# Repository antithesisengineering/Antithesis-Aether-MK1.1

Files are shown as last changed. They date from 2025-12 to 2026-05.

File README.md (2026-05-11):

# Antithesis Aether MK1.1

## Description

The Antithesis Aether is a parallel development of the original. It heavily uses 3D printed parts, drastically reducing cost and complexity. It currently has two major options. An all plastic version in which everything, gantry included is plastic. The main drawback with the plastic gantry version is a reduction in rigidity. This will limit acceleration due to excessive deflection. The second option has an aluminum gantry plate, bed bracket, and uses an extrusion on the X axis. It has the same rigidity on the XY as the MK3.1 and still benefits from a reduction in cost and complexity. It also demonstrates identical print quality to the MK3.1.

The build guide is currently a little outdated but will still provide valuable information. It currently doesn't have a section for the assembly of the metal gantry version. 
Please note: The files for the onboard power supply can be found [**HERE**](https://github.com/antithesisengineering/Antithesis-EPP-LOP-Onboard-Power-Supply) 

## 

## Printed Parts

I would recommend printing the parts out of ABS or ASA with the following settings: 3 walls, 40% Gyroid infill. The only exception is the plastic gantry plate and bed bracket. Those should be printed with as high an infill percentage as possible. I find 75% works pretty well. Ignore this if using the metal gantry plate and bed bracket. You may also want to use mouse ears on some parts if warping is an issue. At least one person has printed theirs out of PLA and has not encountered issues yet.

## 

## Harder to Source Parts

Most of the parts should be easily obtainable. The exceptions to this are the PCB build plate, spring steel sheet, and a few aluminum plates should you decide to build the aluminum version of the gantry. You can source the build plates from PCBWay using a link I will provide. Alternatively, I can provide you one at cost if you contact me on discord. The aluminum plates and spring steel sheet can be obtained from sendcutsend or I can also ship you those at cost as well.

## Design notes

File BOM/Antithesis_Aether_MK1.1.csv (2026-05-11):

Frame
Aether MK1 Frame |  |  |  | Includes everything which doesn't have multiple options i.e the different options for hotends, extruders, gantrys ect. As those options have differing BOMs.
 | Extrusion
 |  | M5 Stamped T-Nut | 24 | Most post assembly T-Nuts should work for this.
 |  | M3 Stamped T-Nut | 20 | Most post assembly T-Nuts should work for this.
 |  | 20x20x200 Extrusion | 1 | Optional if using the onboard PSU. Misumi extrusion is ideal. V-Slot is supported but less ideal as the rails sit into the extrusion slots a bit.
 |  | 20x40x250 Extrusion | 1 | Misumi extrusion is ideal. V-Slot is supported but less ideal as the rails sit into the extrusion slots a bit.
 |  | 40x40x265 Extrusion | 1 | Misumi extrusion is ideal. V-Slot is supported but less ideal as the rails sit into the extrusion slots a bit.
 | Motion
 |  | MGN9Hx180mm Rail and Carriage | 5 | A few places including KB3D offer it in this length.
 |  | 20T Pulley for 6mm Wide Belt and 5mm Shaft | 2
 |  | 20T Idler for 6mm Wide Belt and 5mm Shaft | 2 | Use the gates style ones with the small flang the ones with a bigger flang will not work.
 |  | GT2 6mm Belt 110cm | 1
 |  | 10x4x3 flange Bearing (F623ZZ) | 8
 |  | NEMA 17 48mm | 2 | Use 42STH47-2504AC Speedy Power paired with 5160 Pro drivers for speed. Use 42STH48-1684MAC paired with 2209 drivers for better sensorless homing and quality.
 |  | Nema 17 Integrated Lead Screw 200-210mm | 1 | 200mm to 210mm long will work fine. I would choose based on which one is easier to obtain. These can be obtained from StepperOnine and Amazon.
 |  | 8x22x7 Bearing (608 2RS) | 1
 | Hardware
 |  | M3x6 SHCS | 22
 |  | M3x8 SHCS | 10
 |  | M3x10 SHCS | 2
 |  | M3x12 SHCS | 4
 |  | M3x16 SHCS | 9
 |  | M3x20 SHCS | 2
 |  | M3x8 BHCS | 2
 |  | M3x10 BHCS | 1
 |  | M3x20 BHCS | 4
 |  | M3x5 Ultra Low Profile Screw | 1
 |  | M3x10 CS | 12
 |  | M3 Nylon Insert Nut | 13
 |  | M3 Washer | 24
 |  | M5x10 BHCS | 22
 |  | M5x16 BHCS | 17
 |  | M5x25 BHCS | 2
 |  | M5 Nylon Insert Nut | 3 | You only need one if using the onboard PSU.
 |  | M3x5x4 Heat Set Insert | 15
 |  | Rubber Foot (OpenBuilds or Printed TPU) | 3 | You only need one if using the onboard PSU.
 |  | PC4-M10 Pneumatic Coupling | 1
 |  | 4mm PTFE tubing 83mm(3.25in) | 2 | Used for the spool holder.
 |  | 4mm PTFE tubing 400mm(15.75in) | 1 | Used for the reverse bowden tube.
 |  | 10mm Long x 6mm Hex Standoff | 1 | Used in the middle of the heatbed.
 |  | M3 Knurled Thumb Nuts | 4
 | Bed
 |  | PCB Heater | 1 | Custom PCB heater. All files are on the github and you can have it made by PCBway. I am also currently going to ship them at cost to anyone interested.
 |  | Kapton Tape | 1 | Used to mount the thermistor.
 |  | 3950 Glass Bead Thermistor | 1 | I like Crealitys ones meant for the ender 3. You can order them in a 5 pack.
 |  | 8429T14 Ring Terminals | 2 | For connecting the heated bed cable to the heated bed. It has the mcmaster part number for them.
 |  | Thermal Paste or Grease |  | Used when inserting the thermistor to ensure proper heat transfer.
 |  | Spring Steel Plate | 1 | I get mine cut by send cut send. Needs kapton or your surface of choice adhered on.
 |  | Build Plate Surface | 1 | I like kapton but use any adhesive surface you want.
 |  | Adhesive Magnet | 1 | I like KB3Ds magnets. Needs to be cut to size and needs a hole in the middle for the center screw.
 |  | 16 AWG Silicone Wire |  | For the heated bed cable.
 |  | 20-24 AWG Wire |  | You may need wire to extend the thermistor.
 |  | Heat Shrink Tubing
 |  | Solder
Gantrys
Aluminum Gantry |  |  |  | Probably my preferred option. Its far more rigid than the plastic gantry and allows identical print quality to the MK3.1. Downside being its a bit more complicated and about 20$ more expensive. You also have to source the aluminum parts.
 | Hardware
 |  | M3x6 SHCS | 17
 |  | M3x8 SHCS | 2
 |  | M3x10 SHCS | 2
 |  | M3x12 SHCS | 2
 |  | M3x16 SHCS | 2
 |  | M3x20 SHCS | 8
 |  | M3x10 Set Screw | 1
 |  | M3 Nylon Insert Nut | 2
 |  | M3x5x4 Heat Set Insert | 12
 |  | MakerBeam XL T-Nut (Or Equivalent) | 10
 |  | 15x15x182 Extrusion | 1 | Can be Misumi extrusion or MakerBeam.
 | Sheet Cut Parts
 |  | Aluminum Carriage Plate | 1 | DXF is provided on github. Should be made from 3mm(1/8in) 5052 aluminum. Has a single 90 degree bend. Can be obtained from sendcutsend or I have a small stock I can provide at cost on discord.
 |  | Aluminum Carriage Plate Side | 1 | DXF is provided on github. Should be made from 3mm(1/8in) 5052 aluminum. Get this tumbled unless you want to deburr it yourself. Can be obtained from sendcutsend or I have a small stock I can provide at cost on the discord.
 |  | Aluminum Bed Bracket | 1 | DXF is provided on github. Should be made from 3mm(1/8in) 5052 aluminum. Get this deburred unless you want to deburr it yourself. Can be obtained from sendcutsend or I have a small stock I can provide at cost on the discord.
Plastic Gantry |  |  |  | Easier to source for, cheaper, and simplier since it uses only 3D printed parts in place of aluminum. The downside being it is unsurprisingly way less rigid and will result in more deflection and worse print quality at speed.
 | Hardware
 |  | M3x8 SHCS | 2
 |  | M3x16 SHCS | 2
 |  | M3x20 SHCS | 8
 |  | M3x25 SHCS | 1
 |  | M3x10 CS | 8
 |  | M3x20 CS | 8
 |  | M3x5x4 Heat Set Insert | 20
Controllers
BTT Manta M5P
 | Hardware
 |  | M3x10 SHCS | 8
 |  | M3x20 SHCS | 6
 |  | M3 Nylon Insert Nut | 2 | This is optional. Used only if using an external PSU. Not needed if using an onboard PSU.
 |  | M3x10 CS | 2 | This is optional. Used only if using an external PSU. Not needed if using an onboard PSU.
 |  | M3x5x4 Heat Set Insert | 14
 |  | M5x10 BHCS | 4
 |  | M5 Stamped T-Nut | 4
 |  | Stabilizer Foot (Printed TPU) | 4
 | Components
 |  | Manta M5P | 1
 |  | CB1, CB2 or CM4 | 1 | If using the CB1 make sure to pickup a heat sink too. It runs really hot.
 |  | TMC2209 or TMC5160 Pro Stepper Drivers | 4 | Use 2209s for the Z and E axis. Use 2209s or 5160 pros for the XY. The 5160s are better for speed the 2209s are cheaper and their sensorless homing works better.
 |  | 16GB SD Card | 1 | Unless using EMMc you will need this for the host.
 |  | 5015 24v Blower Fan | 1
 |  | XT60E-F | 1 | This is optional. Used only if using an external PSU. Not needed if using an onboard PSU.
 |  | 6mm(1/4in) Split Cable Sleeve 300mm(12in) | 1 | This is for the bed. | https://www.amazon.com/dp/B07FW5H57B?ref=ppx_yo2ov_dt_b_fed_asin_title&th=1
 |  | 3mm(1/8in) Split Cable Sleeve 150mm(6in) | 3 | These are for the stepper motors. | https://www.amazon.com/dp/B07FWFB9H6?ref=ppx_yo2ov_dt_b_fed_asin_title&th=1
 |  | 13mm(1/2in) Split Cable Sleeve 575mm(22.625in) | 1 | For the main toolhead cable bundle. | https://www.amazon.com/dp/B07FW3GTXB?ref=ppx_yo2ov_dt_b_fed_asin_title&th=1
 |  | Ferrule Crimps |  | Used to terminate the wires for VIN and the heaters.
 |  | 14-16 AWG Wire |  | Cut to length for VIN
 |  | Heat Shrink Tubing
 |  | Solder
Power Supplies
External Power Supply |  |  |  | Sits on the table next to the printer.
 | Hardware
 |  | M3x10 BHCS | 2
 |  | M3 Nut | 2
 |  | M4x6 BHCS | 4
 |  | M4x8 BHCS | 2
 | Components
 |  | IEC-GS-1-100 Receptacle with Fuse | 1
 |  | 5mm Fork Terminal 14-16 AWG | 5
 |  | 5mm Spade Terminal 14-16 AWG | 7
 |  | 14-16 AWG Wire 125mm(5in) | 5 | The long wires from the panel mounted connectors to the power supply should be about 125mm(5in) Too long or short will make it hard to slide the cover on.
 |  | 14-16 AWG Wire 25mm(1in) | 2 | These are for the jumpers to the fuse and from the fuse to the switch.
 |  | 14-16 AWG Wire 300mm(12in) | 2 | These are for the power cable from the PSU to the Control Box.
 |  | Amass XT60 Connector (Female) | 2 | These are for the power cable from the PSU to the Control Box.
 |  | 13mm(1/2in) Split Cable Sleeve 300mm(12in) | 1 | This is for the power cable from the PSU to the Control Box.
 |  | Power Cord C13 | 1
 |  | 8A Fuse | 1
 |  | Meanwell 200W or 350W Power Supply | 1 | Depending on your exact components a 200W PSU might be enough. If you're running a high power hotend or stepper drivers you might need a 350W PSU.
 |  | Heat Shrink Tubing
 |  | Solder
EPP/LOP Onboard Power Supply BOM |  |  |  | Sits under the front of the frame next to the MCU enclosure.
 | Hardware
 |  | M3x8 SHCS | 8
 |  | M3x10 SHCS | 3
 |  | M3x20 SHCS | 2
 |  | M3x10 CS | 2 | Countersunk
 |  | M5x10 BHCS | 4
 |  | M5 Stamped T-Nut | 4
 |  | M3x5x4 Heat Set Insert | 11
 | Components
 |  | 24V EPP or LOP Power Supply | 1 | I would advise getting the LOP power supply unless you already have a EPP series on hand. The LOP is newer, smaller, and the 300W LOP is the same price as a 200W EPP. Either the 200W or 300W one will work fine. | https://www.digikey.com/en/products/detail/mean-well-usa-inc/epp-200-24/7703124 | https://www.digikey.com/en/products/detail/mean-well-usa-inc/LOP-200-24/22040939 | https://www.digikey.com/en/products/detail/mean-well-usa-inc/LOP-300-24/22040910
 |  | VHR-3N | 1 | 3 Pin Connector for the AC in. These are a little hard to find | https://www.digikey.com/en/products/detail/jst-sales-america-inc/VHR-3N/608625
 |  | VHR-6N | 1 | 6 Pin Connector for the DC out. These are a little hard to find | https://www.digikey.com/en/products/detail/jst-sales-america-inc/VHR-6N/608628
 |  | SVH-41T-P1.1 | 4 | Crimped contacts for the 18 AWG AC in and 16 AWG DC out wires. You should probably buy a few extra. | https://www.digikey.com/en/products/detail/jst-sales-america-inc/SVH-41T-P1-1/608760
 |  | SVH-21T-P1.1 | 2 | Crimped contacts for the 22 AWG JST lead for the cooling fan. Optional if you decide to power the fan from the MCU board. You should probably buy a few extra. | https://www.digikey.com/en/products/detail/jst-sales-america-inc/SVH-21T-P1-1/527368
 |  | JST-XH 2.54mm Plug Lead | 1 | Used to connect the fan to the 24V DC out. Needs to be 22 AWG. Optional if you decide to power the fan from the MCU board. | https://www.amazon.com/dp/B096DSGJLD?th=1
 |  | C14 Inlet with Switch | 1 | The important thing is to make sure its the correct style as seen in the instructions and link. | https://www.amazon.com/dp/B0BCYYNRGP?th=1
 |  | C13 Power Cord | 1 | Buy which ever length you need. | https://www.amazon.com/Standard-Electronics-Computer-Printer-Monitor/dp/B09VRLJD7J/ref=1
 |  | 5015 24V Blower Fan | 1 | Should be 24V unless you plan to power it off the PSU boards specific fan connector in which case you will need 12V. | https://www.amazon.com/GDSTIME-Cooling-Brushless-Hydraulic-Humidifier/dp/B0DLKNMH5R/ref=1
 |  | 2.5mm(.1in) Wide Zip Tie | 1
 |  | 16 AWG Wire |  | Cut to length for 24V DC out. While the amount needed varies 175mm(7in) Should be enough for most setups.
 |  | 6mm(1/4in) Split Cable Sleeve 25mm(1in) |  | This is for the gap between the PSU and MCU enclosures. | https://www.amazon.com/dp/B07FW5H57B?ref=ppx_yo2ov_dt_b_fed_asin_title&th=1
Extruder Adapters
Orbiter Extruder Adapter
 | Hardware
 |  | M3x10 SHCS | 2
 |  | M3x5x4 Heat Set Insert | 6
 | Components
 |  | Orbiter v2.5 | 1
LGX Extruder Adapter
 | Hardware
 |  | M3x8 SHCS | 4
 |  | M3x12 SHCS | 2
 |  | M3x5x4 Heat Set Insert | 4
 | Components
 |  | LGX | 1
Galileo 2 Extruder Adapter
 | Hardware
 |  | M3x12 SHCS | 2
 |  | M3x5x4 Heat Set Insert | 6
 | Components
 |  | Galileo 2 Standalone | 1
Hotend Adapters
Bambu X1 Style Hotend Adapter
 | Hardware
 |  | M2.5x6 SHCS | 2
 |  | M3x12 SHCS | 2
 |  | M3x20 SHCS | 6
 |  | M3x25 SHCS | 2
 |  | M3x12 SHCS | 4
 |  | M3x5x4 Heat Set Insert | 12
 | Components
 |  | X1 Style Hotend | 1 | This could be the OEM or any of its many replacements
 |  | 5015 24v Blower Fan | 2
 |  | 4010 24v Axial Fan | 1
 |  | Fan Extension Cable | 3 | I like E3Ds cables as they come with micro fit connectors.
 |  | Thermistor Extension Cable | 1 | I like E3Ds cables as they come with micro fit connectors.
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

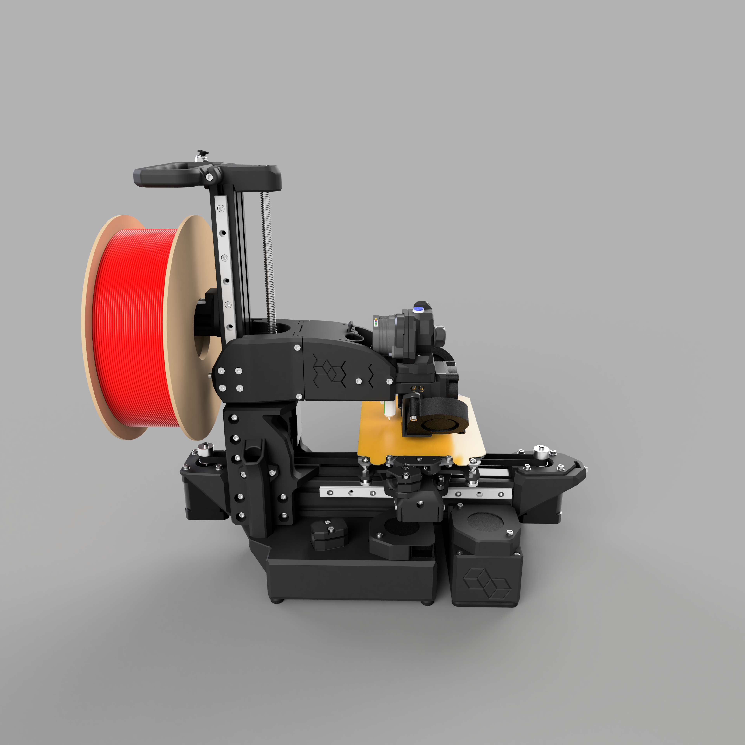
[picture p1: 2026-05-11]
PICTURES/AetherMK1.1.png

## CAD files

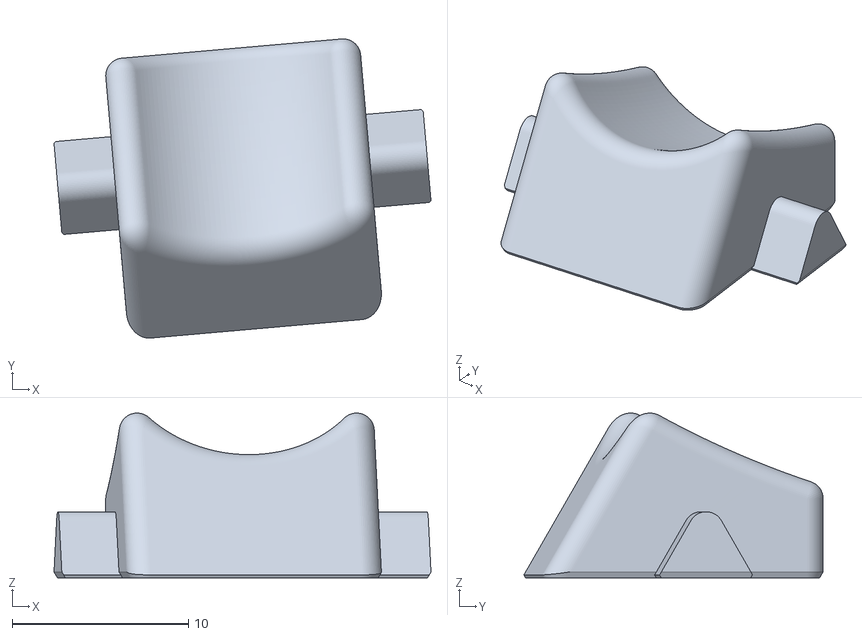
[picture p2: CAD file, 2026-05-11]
STLS/Main Cable Conduit 2.stl
21.4 x 17.0 x 9.34

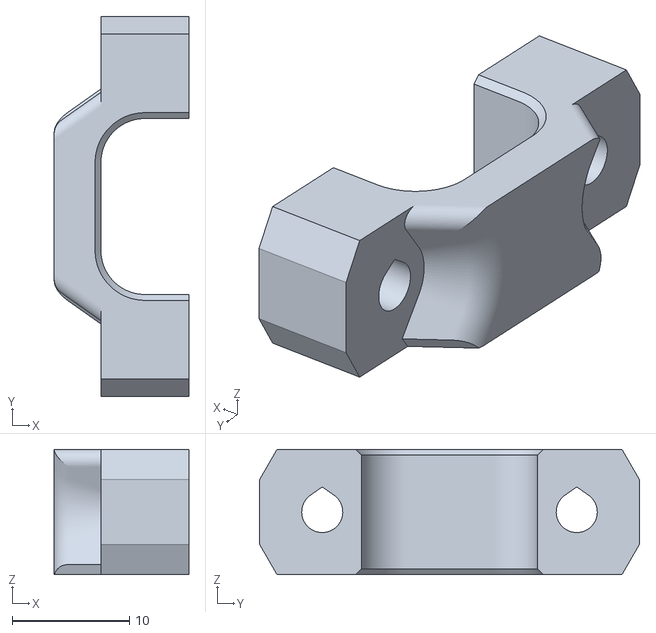
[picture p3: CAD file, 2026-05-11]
STLS/Controllers/M5P/Enclosure Main Cable Clamp.stl
11.5 x 32.4 x 10.7

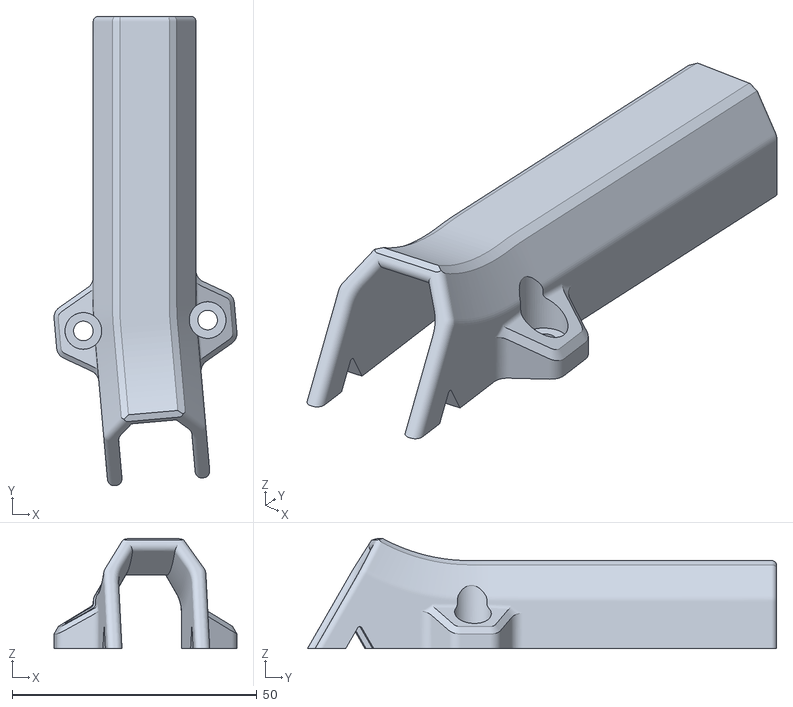
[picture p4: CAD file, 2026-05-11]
STLS/Main Cable Conduit.stl
37.4 x 95.9 x 22.5

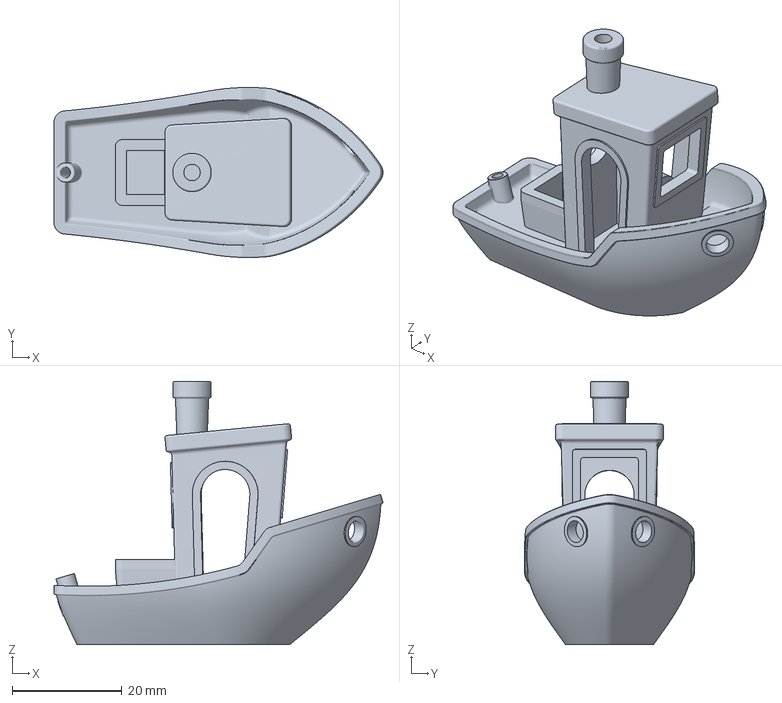
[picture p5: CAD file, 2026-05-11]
PRINT PROFILES/PLA_MEDIUM.3mf
60.0 x 31.0 x 48.0 mm

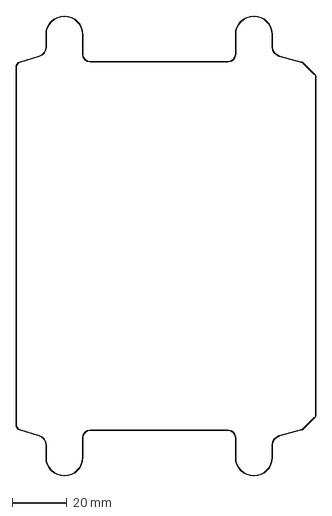
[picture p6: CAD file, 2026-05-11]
SHEET CUT PARTS/Flex_Plate_(Reversible).dxf
110.0 x 168.5 mm

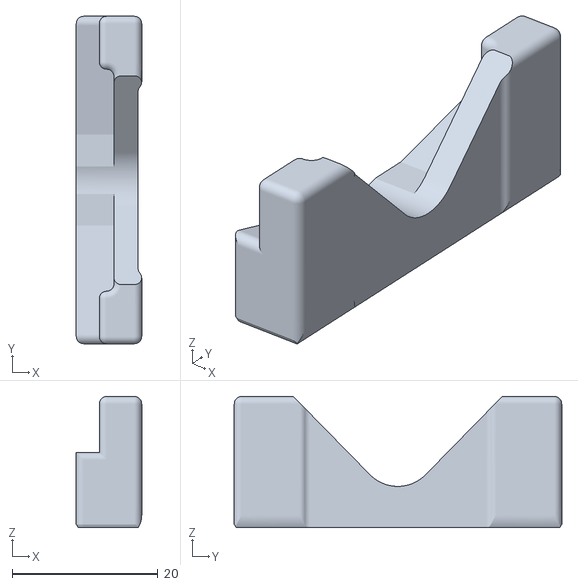
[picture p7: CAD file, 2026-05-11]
STLS/Build Helpers/Aluminum Gantry Plate Tool 1.stl
9.00 x 45.0 x 18.0

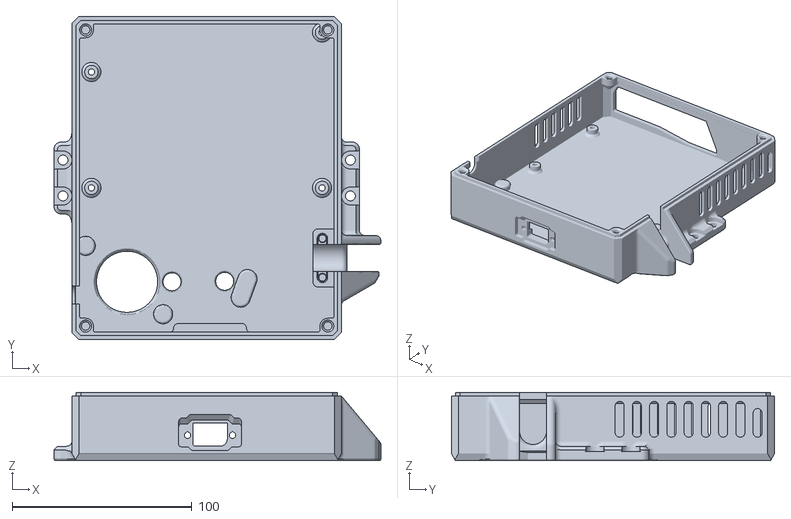
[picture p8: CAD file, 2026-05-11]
STLS/Controllers/M5P/Manta M5P Enclosure (External PSU).stl
182.0 x 180.0 x 38.0

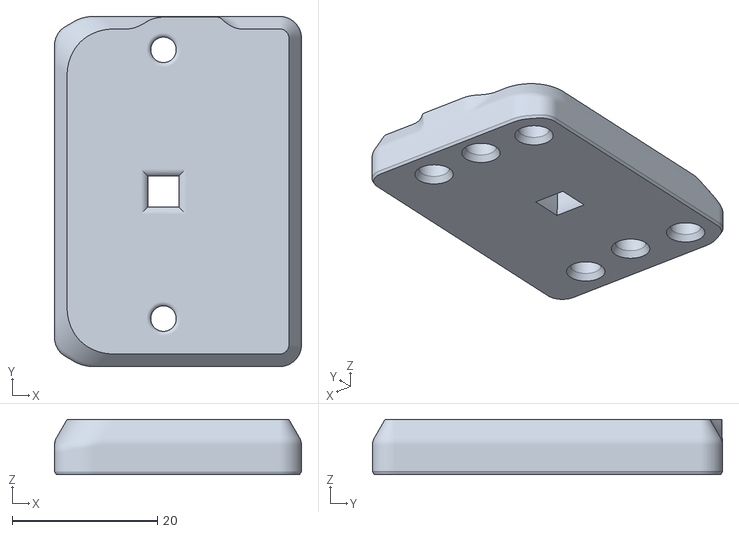
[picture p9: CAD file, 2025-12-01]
STLS/Extruder Adapters/Orbiter V2.5 Extruder Adapter.stl
34.0 x 48.2 x 7.60

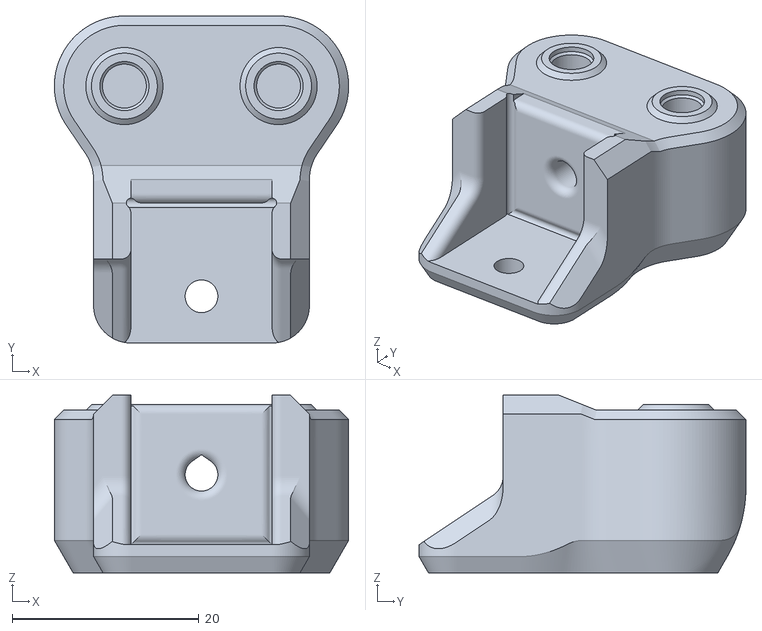
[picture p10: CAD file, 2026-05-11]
STLS/Gantrys/Aluminum/X Axis Idler Mount (Extrusion).stl
31.5 x 35.0 x 19.0

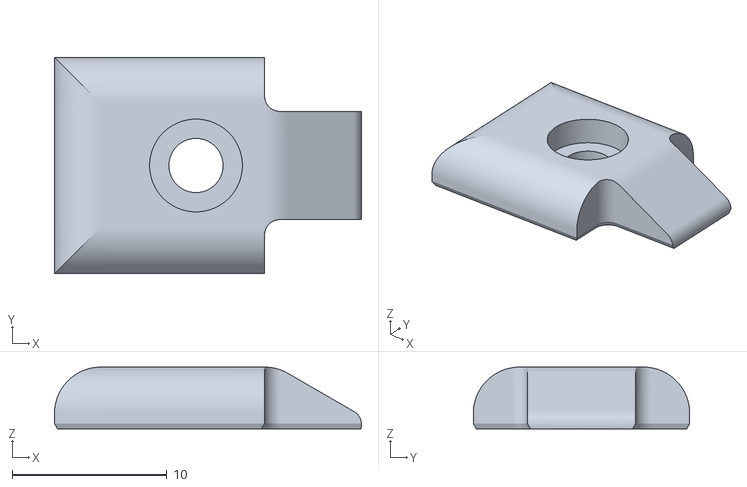
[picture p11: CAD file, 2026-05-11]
STLS/Gantrys/Plastic/X Axis Belt Block Clamp x2.stl
19.9 x 14.0 x 4.00

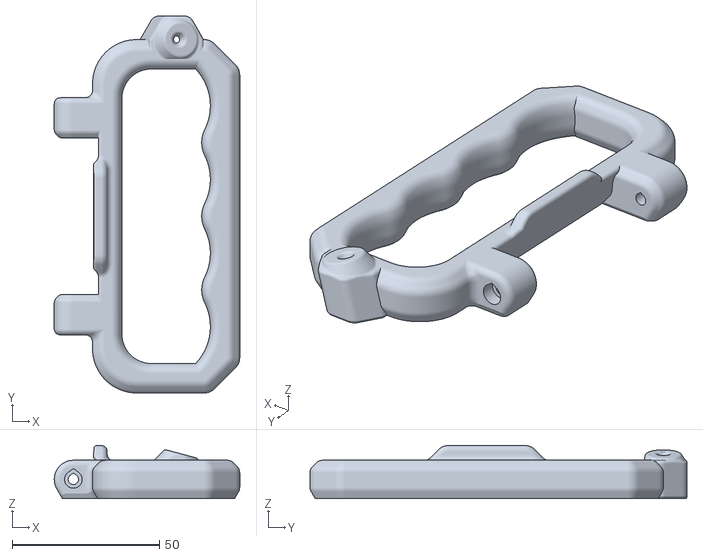
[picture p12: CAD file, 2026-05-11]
STLS/Handle with PTFE Tube Mount (Fixed).stl
63.0 x 128.0 x 18.0

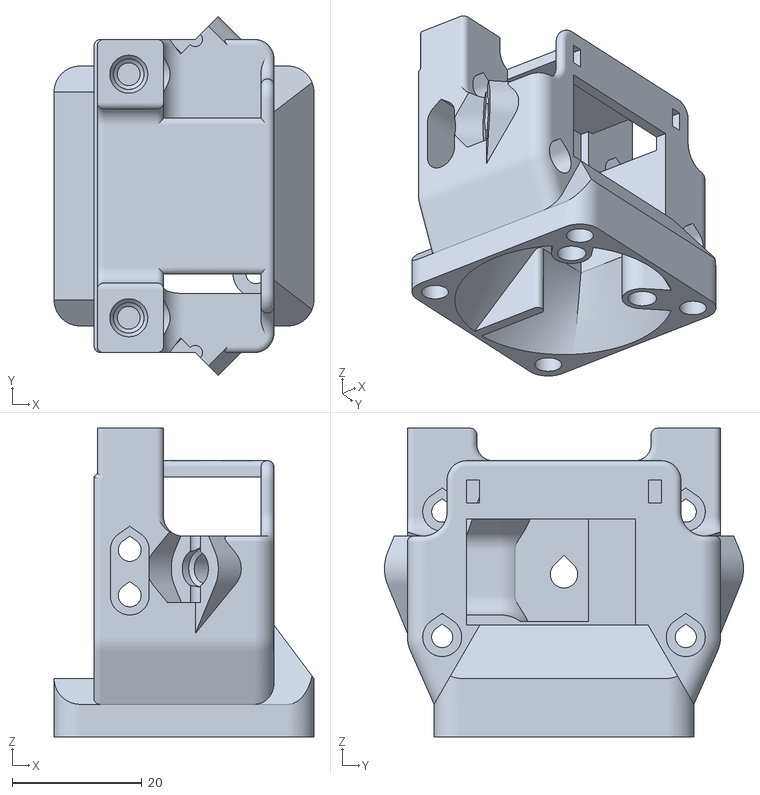
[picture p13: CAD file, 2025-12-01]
STLS/Hotend Adapters/Bambu Style/Phaetus Conch Hotend Adapter.stl
40.0 x 55.3 x 47.5

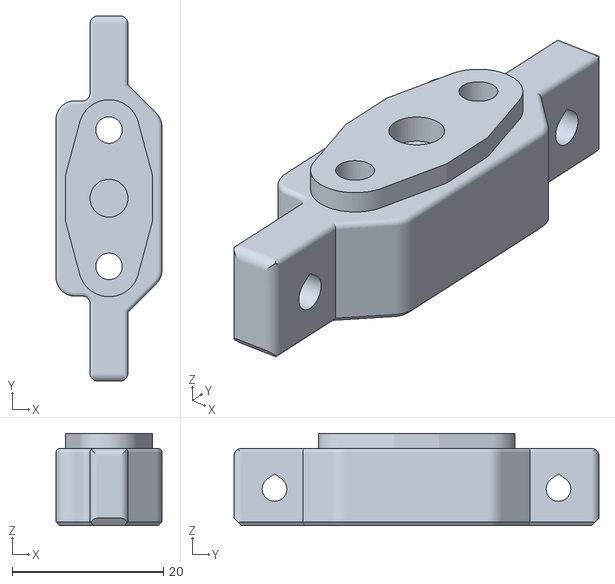
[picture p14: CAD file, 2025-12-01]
STLS/Hotend Adapters/Mosquito/BL Touch Probe Mount.stl
14.0 x 48.2 x 12.2

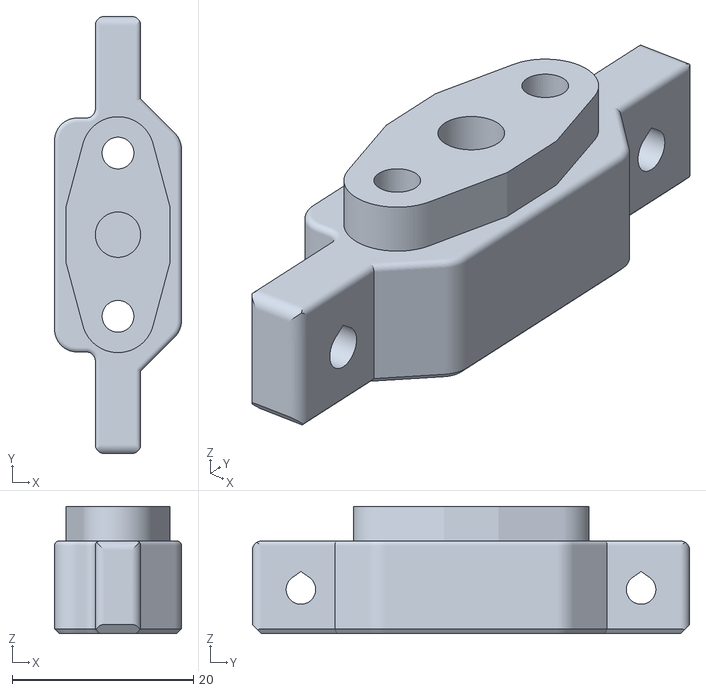
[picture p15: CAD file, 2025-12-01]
STLS/Hotend Adapters/Revo/BL Touch Probe Mount.stl
14.0 x 48.2 x 14.0

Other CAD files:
STLS/Hotend Adapters/Teakettle/Part Cooling Fan Mount - Left.stl
PRINT PROFILES/PLA_QUALITY.3mf
SHEET CUT PARTS/Bed_Bracket.dxf
STLS/Build Helpers/Bearing Lockring Wrench.stl
PREVIOUS VERSIONS/MK1/SHEET CUT PARTS/Bed_Bracket.dxf
PREVIOUS VERSIONS/MK1/SHEET CUT PARTS/Gantry_Plate.dxf
PREVIOUS VERSIONS/MK1/SHEET CUT PARTS/Gantry_Plate_Side.dxf
PREVIOUS VERSIONS/MK1/STLS/Bed Cable Cover Bottom.stl
PREVIOUS VERSIONS/MK1/STLS/Bed Cable Cover Top.stl
PREVIOUS VERSIONS/MK1/STLS/Belt Tensioner.stl
PREVIOUS VERSIONS/MK1/STLS/Build Helpers/15x15 Extrusion MGN9 Alignment Tool.stl
PREVIOUS VERSIONS/MK1/STLS/Build Helpers/20x20 Extrusion MGN9 Alignment Tool.stl
PREVIOUS VERSIONS/MK1/STLS/Build Helpers/20x40 Extrusion MGN9 Alignment Tool.stl
PREVIOUS VERSIONS/MK1/STLS/Build Helpers/Aluminum Gantry Plate Tool 1.stl
PREVIOUS VERSIONS/MK1/STLS/Build Helpers/Aluminum Gantry Plate Tool 2.stl
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

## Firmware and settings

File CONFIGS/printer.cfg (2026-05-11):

# Config is for an Antithesis Aether MK1.1 with a BTT Manta M5P and CB2 #

[include mainsail.cfg]
#[include MAISA.cfg]
#[include ADXL345.cfg]



[mcu]
serial: /dev/serial/by-id/usb-Klipper



[printer]
kinematics: corexy
max_velocity: 500
max_accel: 20000
minimum_cruise_ratio: 0.5
max_z_velocity: 25
max_z_accel: 100
square_corner_velocity: 5



[stepper_x]
step_pin: PE6
dir_pin: PE5
enable_pin: !PC14
endstop_pin: tmc2209_stepper_x:virtual_endstop
microsteps: 32
rotation_distance: 40
full_steps_per_rotation: 400
position_endstop: -2.5
position_min: -2.5
position_max: 130
homing_retract_dist: 0
homing_speed: 40

[tmc2209 stepper_x]
uart_pin: PC13
diag_pin: ^PF4
driver_SGTHRS: 120
sense_resistor: 0.110
run_current: 1.1
interpolate: False
stealthchop_threshold: 0



[stepper_y]
step_pin: PE2
dir_pin: !PE1
enable_pin: !PE4
endstop_pin: tmc2209_stepper_y:virtual_endstop
microsteps: 32
rotation_distance: 40
full_steps_per_rotation: 400
position_endstop: -5
position_min: -5
position_max: 100
homing_retract_dist: 0
homing_speed: 40

[tmc2209 stepper_y]
uart_pin: PE3
diag_pin: ^PF3
driver_SGTHRS: 110
sense_resistor: 0.110
run_current: 1.1
interpolate: False
stealthchop_threshold: 0



[stepper_z]
step_pin: PB8
dir_pin: PB7
enable_pin: !PE0
endstop_pin: probe:z_virtual_endstop
microsteps: 32
rotation_distance: 4
full_steps_per_rotation: 200
position_min: -1
position_max: 115.5
homing_retract_dist: 5
homing_speed: 25
second_homing_speed: 2.5

[tmc2209 stepper_z]
uart_pin: PB9
#diag_pin: PC3
sense_resistor: 0.110
run_current: 1.0
interpolate: False
stealthchop_threshold: 0



[extruder]
step_pin: PB4
dir_pin: PB3
enable_pin: !PB6
heater_pin: PA0
sensor_pin: PB0
sensor_type: ATC Semitec 104GT-2
control: pid
pid_Kp: 48.881
pid_Ki: 18.104
pid_Kd: 32.995
min_temp: 15
max_temp: 280
microsteps: 64
rotation_distance: 47.088
gear_ratio: 9:1
nozzle_diameter: 0.400
filament_diameter: 1.750
max_extrude_only_distance: 500
max_extrude_cross_section: 100
max_extrude_only_velocity: 120
pressure_advance: 0.04
pressure_advance_smooth_time: 0.03

[tmc2209 extruder]
uart_pin: PB5
#diag_pin: PC2
sense_resistor: 0.110
run_current: 0.7
interpolate: True
stealthchop_threshold: 0
driver_TBL: 0
driver_HEND: 6
driver_HSTRT: 7
driver_TOFF: 4



[heater_bed]
heater_pin: PF5
sensor_pin: PB1
sensor_type: Generic 3950
control: pid
pid_Kp: 56.859 
pid_Ki: 1.934 
pid_Kd: 417.914
min_temp: 15
max_temp: 115



[bltouch]
sensor_pin: PD13
control_pin: PD12
pin_move_time: 0.7
x_offset: 0
y_offset: 25
z_offset: 2.20
speed: 5
lift_speed: 20
stow_on_each_sample: False



[bed_mesh]
speed: 250
horizontal_move_z: 5.0
mesh_min: 2.5, 21
mesh_max: 127.5, 97.5
probe_count: 5, 3
fade_start: 1.0
fade_end: 5.0



[multi_pin fan]
pins: PF7, PF9

[fan]
pin: multi_pin:fan
max_power: 1.0
shutdown_speed: 0
cycle_time: 0.01
kick_start_time: 0.1
off_below: 0.10



[heater_fan heatbreak_cooling_fan]
pin: PF6
max_power:1.0
shutdown_speed: 1.0
heater: extruder
heater_temp: 50
fan_speed: 1.0



[controller_fan mcu_fan]
pin: PF8
max_power: 1.0
shutdown_speed: 0
cycle_time: 0.01
kick_start_time: 0.1
off_below: 0.15



[homing_override]
axes: xyz
set_position_z: 0
gcode:   
    {% set HOME_ACC = 1000 %}   
    {% set CONFIG_ACC = printer.configfile.settings['printer'] %}
    {% set NORMAL_ACC = CONFIG_ACC.max_accel %}
    SET_VELOCITY_LIMIT ACCEL={HOME_ACC}
    SET_STEPPER_ENABLE STEPPER=stepper_x ENABLE=1
    SET_STEPPER_ENABLE STEPPER=stepper_y ENABLE=1
    G4 P2000
    G90
    G0 Z4 F900
    {% set HOME_CUR = 0.5 %}
    {% set CONFIG_CURX = printer.configfile.settings['tmc2209 stepper_x'] %}
    {% set NORMAL_CURX = CONFIG_CURX.run_current %}
    {% set CONFIG_CURY = printer.configfile.settings['tmc2209 stepper_y'] %}
    {% set NORMAL_CURY = CONFIG_CURY.run_current %}
    SET_TMC_CURRENT STEPPER=stepper_x CURRENT={HOME_CUR}
    SET_TMC_CURRENT STEPPER=stepper_y CURRENT={HOME_CUR}
    G4 P2000
    G28 Y0
    G90
    G1 Y0 F1200
    G4 P2000
    G28 X0
    G90
    G1 X0 F1200
    SET_TMC_CURRENT STEPPER=stepper_y CURRENT={NORMAL_CURY}
    SET_TMC_CURRENT STEPPER=stepper_x CURRENT={NORMAL_CURY}
    G4 P1000
    G0 X65 Y25 F6000
    G28 Z0
    G0 Z10 F900
    SET_VELOCITY_LIMIT ACCEL={NORMAL_ACC}



[input_shaper]
shaper_type_x = ei
shaper_freq_x = 65.0
shaper_type_y = ei
shaper_freq_y = 57.0



[gcode_macro _CLIENT_VARIABLE]
variable_use_custom_pos   : True ; #use custom park coordinates for x,y [True/False]
variable_custom_park_x    : 65.0   ; #custom x position; value must be within your defined min and max of X
variable_custom_park_y    : 100.0   ; #custom y position; value must be within your defined min and max of Y
variable_custom_park_dz   : 2.0   ; #custom dz value; the value in mm to lift the nozzle when move to park position
variable_retract          : 1.0   ; #the value to retract while PAUSE
variable_cancel_retract   : 5.0   ; #the value to retract while CANCEL_PRINT
variable_speed_retract    : 35.0  ; #retract speed in mm/s
variable_unretract        : 1.0   ; #the value to unretract while RESUME
variable_speed_unretract  : 35.0  ; #unretract speed in mm/s
variable_speed_hop        : 15.0  ; #z move speed in mm/s
variable_speed_move       : 100.0 ; #move speed in mm/s
variable_park_at_cancel   : True ; #allow to move the toolhead to park while execute CANCEL_PRINT [True/False]
variable_park_at_cancel_x : None  ; #different park position during CANCEL_PRINT [None/Position as Float]; park_at_cancel must be True
variable_park_at_cancel_y : None  ; #different park position during CANCEL_PRINT [None/Position as Float]; park_at_cancel must be True
## !!! Caution [firmware_retraction] must be defined in the printer.cfg if you set use_fw_retract: True !!!
variable_use_fw_retract   : False ; #use fw_retraction instead of the manual version [True/False]
variable_idle_timeout     : 0     ; #time in sec until idle_timeout kicks in. Value 0 means that no value will be set or restored
gcode:

[include moonraker_obico_macros.cfg]
